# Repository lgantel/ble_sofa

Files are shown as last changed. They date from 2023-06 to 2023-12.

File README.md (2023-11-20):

# BLE Sofa
Control module for CIAR sofa using custom BLE interface.

## Overview

The sofa command box is powered over a 4 pins RJ9 connector. The voltage measured at the command box input is 29V. It is provided by the motor (LM35_05) which gets its power from the PS10 adapter (29V - 2A).

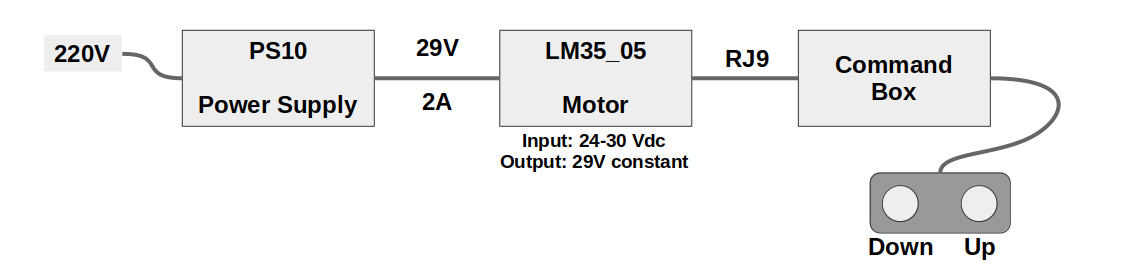
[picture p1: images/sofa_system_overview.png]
Sofa System Overview


The command box has three cable inputs:
- The RJ9 connector for power supply and motor commands
- The left input (J1) connected to the sensitive button; It corresponds to the Down command.
- The right input (J3) connected to the other sensitive button; It corresponds to the Up command.

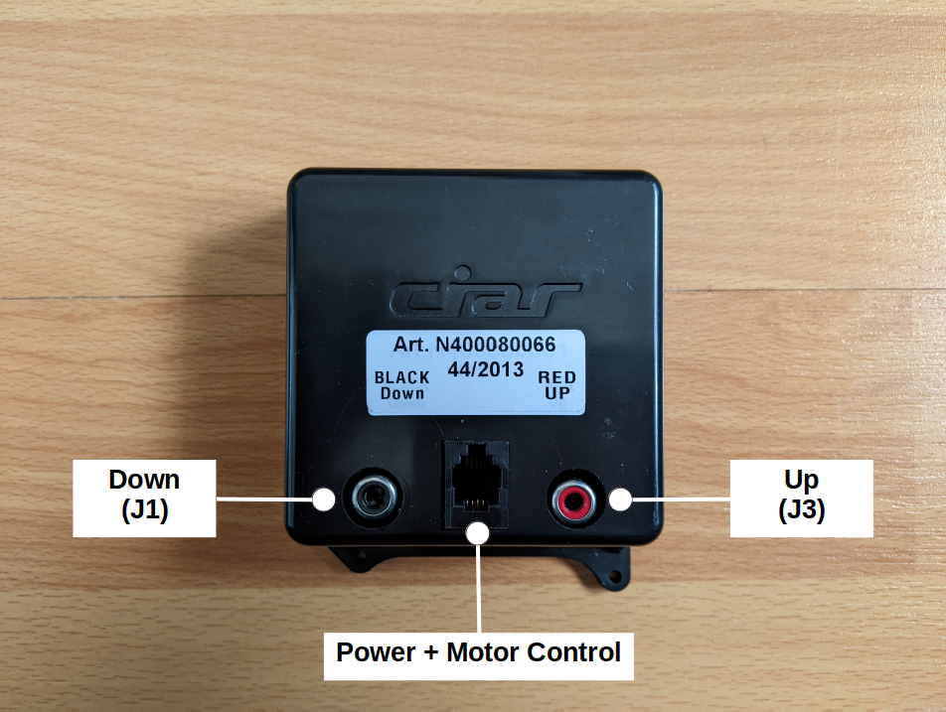
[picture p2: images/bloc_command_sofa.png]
Bloc Command Sofa


## Power Supply and Motor Commands

The RJ9 connector provides 4 wires connection which supplies power from the motor to the control box, and Up and Down commands from the control box to the motor.

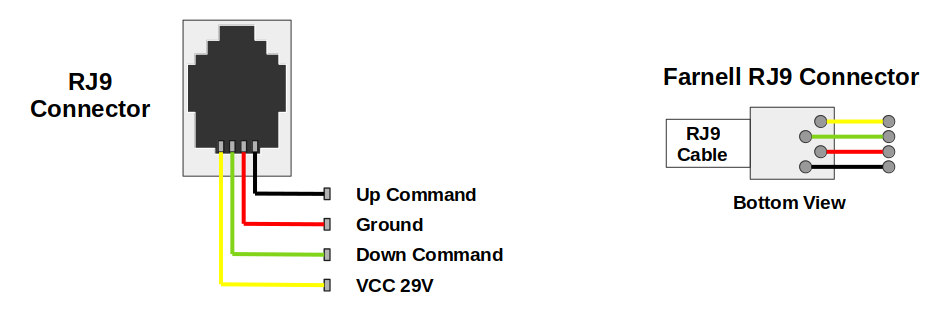
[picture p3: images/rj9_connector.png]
RJ9 Connector


## Issue with the current system

Currently the command box is connected to the Up and Down button with electrical wires. The issue comes when moving the sofa up and down, the cables are compressed by the mechanical part and end up being damaged.

## Replacement Solution

A replacement solution has been specified to allow the user to control the sofa using a wireless BLE application. The system would be based on a Raspberry Pi Pico W module which permits to easily control the motor through two electrical relays, and to receive commands from the user via the Bluetooth stack.

<p float="left">
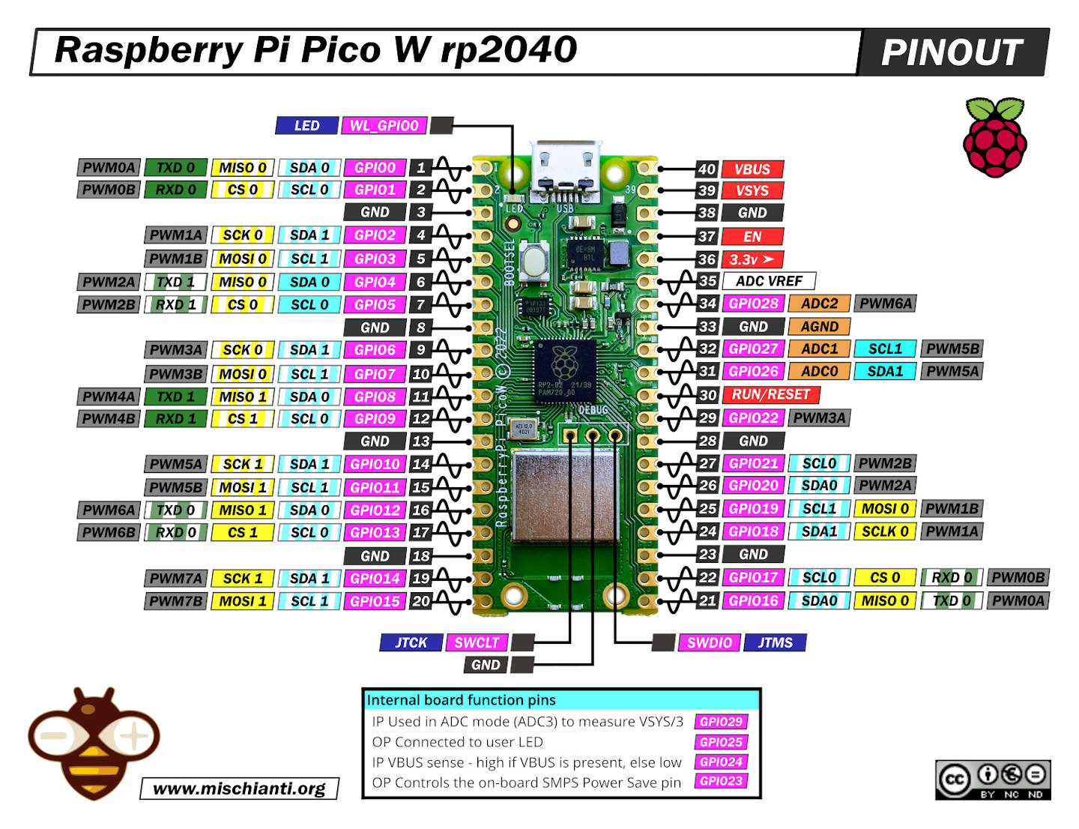
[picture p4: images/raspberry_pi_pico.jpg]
Raspberry Pi Pico W
  
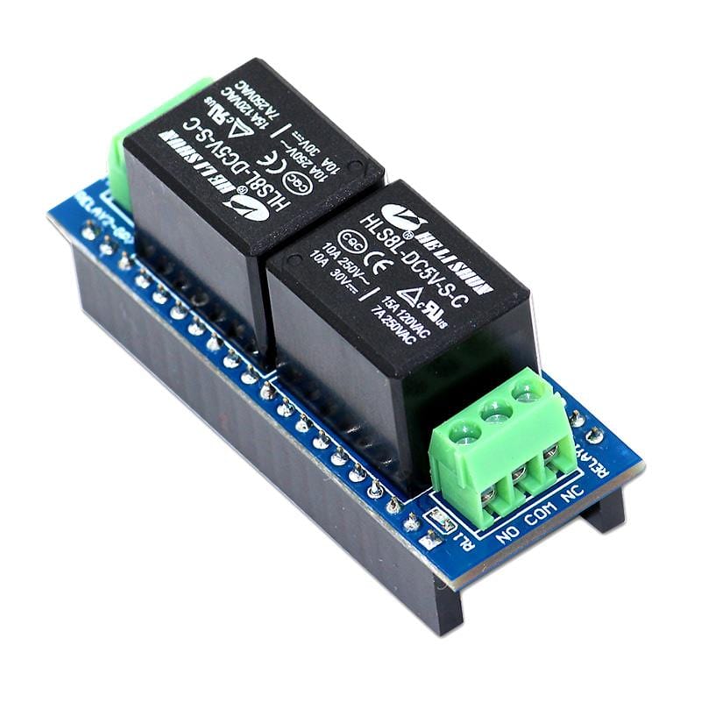
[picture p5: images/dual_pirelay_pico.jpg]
Dual PiRelay for RPi Pico
  
</p>

# Tools Setup

## Get the SDK and examples

```bash
cd pico
git clone https://github.com/raspberrypi/pico-sdk.git --branch master
cd pico-sdk
git submodule update --init
cd ..
git clone https://github.com/raspberrypi/pico-examples.git --branch master
```

## Install the toolchain

```bash
sudo apt update
sudo apt install cmake gcc-arm-none-eabi libnewlib-arm-none-eabi build-essential libstdc++-arm-none-eabi-newlib
```

In the bashrc file, export the path to the SDK:
```bash
#
# RPi Pico SDK
#
export PICO_SDK_PATH=/home/laurent/Projects/lgantel/ble_sofa/pico/pico-sdk
```

# Example Projects

```bash
cd pico/workspace
mkdir build
cd build
```

The following examples can be built:

- [LED Control](doc/example_projects.md#led-control)
- [BLE Control](doc/example_projects.md#ble-control)
- [Relay Control](doc/example_projects.md#relay-control)

# BLE Sofa Application

- [BLE Sofa Application Documentation](doc/ble_sofa_app.md#ble_sofa_app)

# Resources

## Raspberry Pi Pico

* Raspberry Pi Pico power pins information:

https://dronebotworkshop.com/pi-pico/

* A nice development kit PCB example for Raspberry Pi Pico:

https://01001000.xyz/2021-02-13-Raspberry-Pi-Pico-dev-board-Kiwikit/

* C library for LCD OLED:

https://github.com/martinkooij/pi-pico-ss-oled

* Information on the debug probes:

https://www.framboise314.fr/tout-nouveau-la-sonde-de-debogage-raspberry-pi-debug-probe/

* Kicad symbol and footprint models:

https://github.com/bdubs-astro/Raspberry_Pi_Pico_W_Kicad_Files

## Bluetooth Low Energy

* Bluetooth BLE resources:

http://tvaira.free.fr/bts-sn/activites/activite-ble/bluetooth-ble.html#gatt-et-att

https://novelbits.io/bluetooth-gatt-services-characteristics/

https://www.jaredwolff.com/get-started-with-bluetooth-low-energy/

https://punchthrough.com/android-ble-guide/

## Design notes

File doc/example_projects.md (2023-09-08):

# Example Projects

## LED Control

### Block Diagram

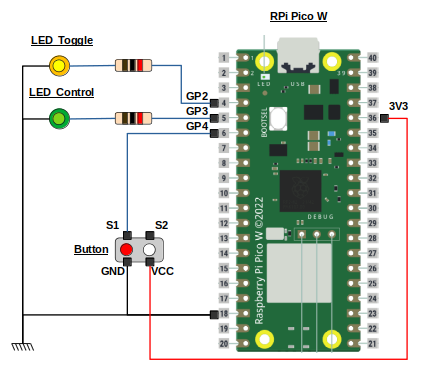
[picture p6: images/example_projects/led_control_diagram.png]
LED Control Diagram


### Description

- LED_Toggle is controlled via GP2 and is toggled every 500 ms.
- LED_Control is controlled via GP3 and its status is dependent of the state of the S1 button. In our case, the S1 button is active-low.

### Compilation

```bash
cmake ..
make -j4 led_control
```

## BLE Control

### Block Diagram

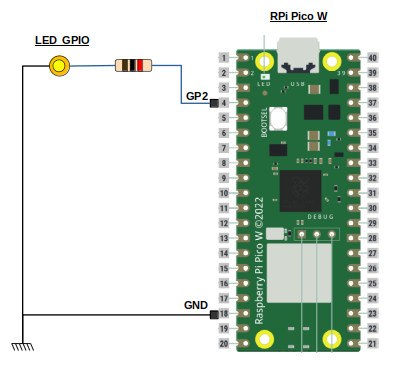
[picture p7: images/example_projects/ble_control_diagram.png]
BLE Control Diagram


### Description

In this example project, the BLE stack is activated and a GATT profile is provided by the Raspberry Pi Pico.

### Compilation

```bash
cmake -DPICO_BOARD=pico_w ..
make -j4 ble_control
```

### Test

1. Test detection on Linux

Scan of the available BLE devices:
```bash
sudo hcitool lescan
LE Scan ...
43:43:A2:12:1F:AC ble-control
```

2. Connection in interactive mode to the BLE Control device:
```bash
sudo gatttool -b 43:43:A2:12:1F:AC -I
[43:43:A2:12:1F:AC][LE]> connect
Attempting to connect to 43:43:A2:12:1F:AC
Connection successful
```

3. Read the primary services provided by the BLE Control device. Our custom service has the UUID 0000ff10-0000-1000-8000-00805f9b34fb. It defines a characteristic that can be written to control the LED state (UUID 0000ff11-0000-1000-8000-00805f9b34fb):
```bash
> primary
attr handle: 0x0001, end grp handle: 0x0003 uuid: 00001800-0000-1000-8000-00805f9b34fb  <-- Generic Access Profile
attr handle: 0x0004, end grp handle: 0x0006 uuid: 0000ff10-0000-1000-8000-00805f9b34fb  <-- Our control service
> char-desc 0x0001
handle: 0x0001, uuid: 00002800-0000-1000-8000-00805f9b34fb  <-- Primary service
handle: 0x0002, uuid: 00002803-0000-1000-8000-00805f9b34fb  <-- Characteristic information
handle: 0x0003, uuid: 00002a00-0000-1000-8000-00805f9b34fb  <-- Generic Access service (name)
handle: 0x0004, uuid: 00002800-0000-1000-8000-00805f9b34fb  <-- Primary service
handle: 0x0005, uuid: 00002803-0000-1000-8000-00805f9b34fb  <-- Characteristic information
handle: 0x0006, uuid: 0000ff11-0000-1000-8000-00805f9b34fb  <-- LED control custom characteristic
```

4. The value of the characteristic can be read with the char-read-hnd command:
```bash
char-read-hnd 0x0006
Characteristic value/descriptor: 00
```

5. The characteristic being a write-without-response characteristic, we use the char-write-cmd command to write on it:
```bash
# Set the LED on
char-write-cmd 0x0006 01
# Set the LED off
char-write-cmd 0x0006 00
```

### Android Application

An Android application has been developped to test the BLE Control example via a smartphone. The application is available in android/workspace/ble_control/.

## Relay Control

### Block Diagram

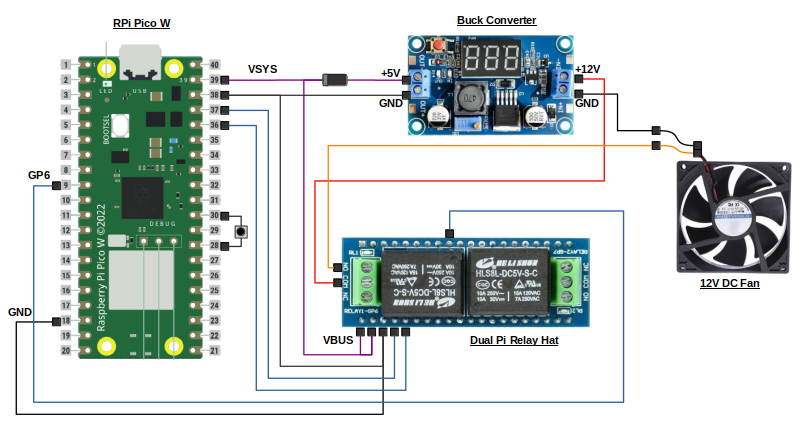
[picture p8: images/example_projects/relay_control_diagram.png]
Relay Control Diagram


### Description

In this example project, the Raspberry Pi Pico controls the relay 1 of the Dual Pi Relay Hat via the GPIO 6. 
- The relay is connected to a 12V DC fan
- The relay is turned on during 5 seconds
- The relay is then turned off for 3 seconds

### Compilation

```bash
cmake -DPICO_BOARD=pico_w ..
make -j4 relay_control
```

### References

- Pico Dual Channel Relay Hat

Information about the relay hat can be found here:

[https://learn.sb-components.co.uk/Pico-Dual-Channel-Relay-Hat]

and there:

[https://github.com/sbcshop/Pico-dual-channel-Relay-HAT]

- Known Issues with Relays:

[https://electronics.stackexchange.com/questions/631931/ac-current-on-relay-causes-pi-pico-to-reboot-continuously]

[https://forums.raspberrypi.com/viewtopic.php?t=322133]

[https://forums.raspberrypi.com/viewtopic.php?t=64595]

[https://forums.raspberrypi.com/viewtopic.php?f=91&t=83372&p=1225448#p1225448]

- Circuit for 29v to 5v converter:

[https://electronics.stackexchange.com/questions/588770/logic-level-converter-from-29v-to-5v-schematic]

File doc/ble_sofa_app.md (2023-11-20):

# BLE Sofa Application

## Block Diagram

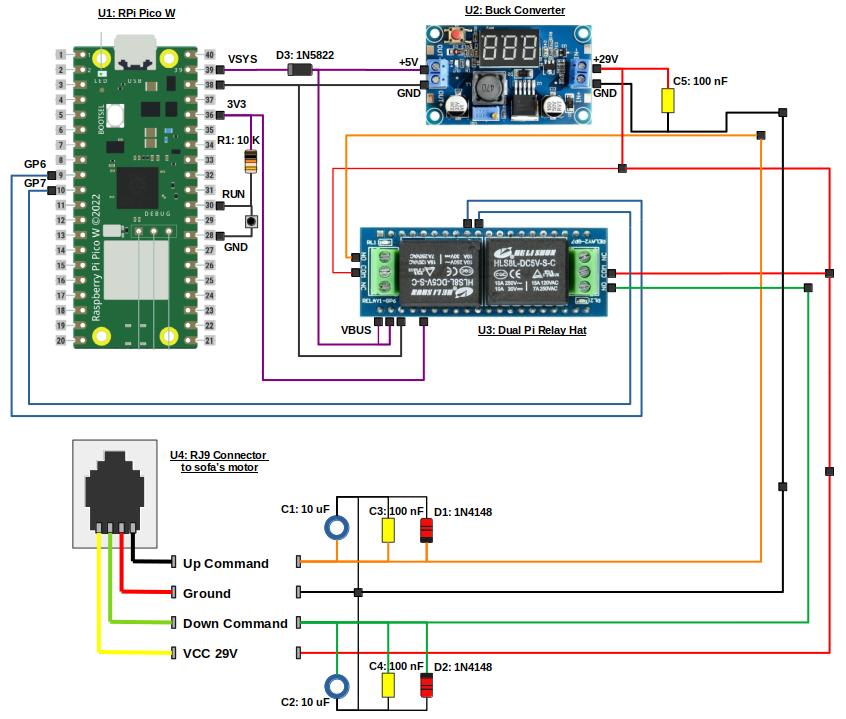
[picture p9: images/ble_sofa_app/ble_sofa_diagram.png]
BLE Sofa Diagram


## Description

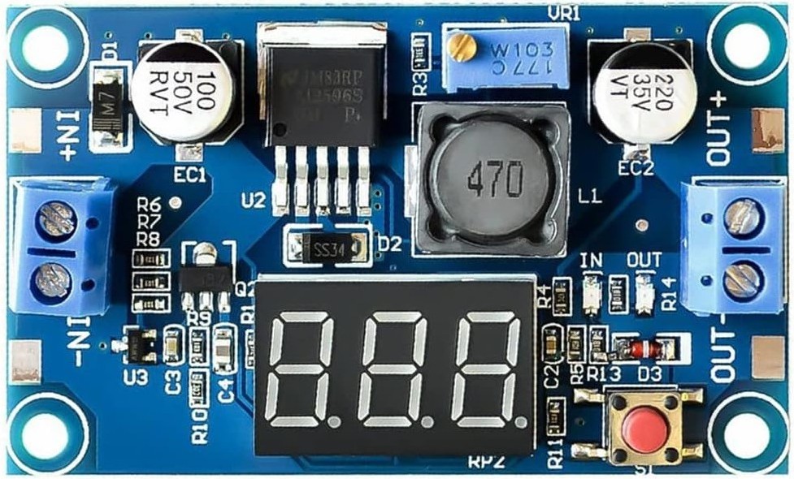
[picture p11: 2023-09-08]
images/buck_converter.jpg

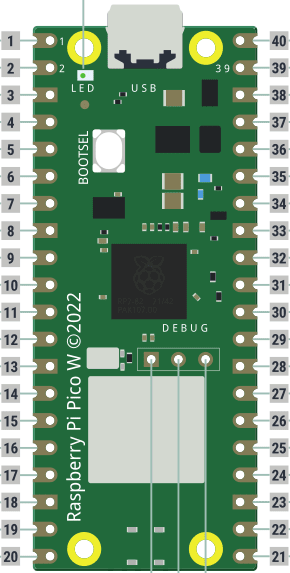
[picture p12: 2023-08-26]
images/RPi-Pico-W.png

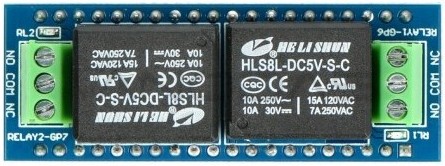
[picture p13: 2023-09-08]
images/dual_pirelay_pico_top.jpg

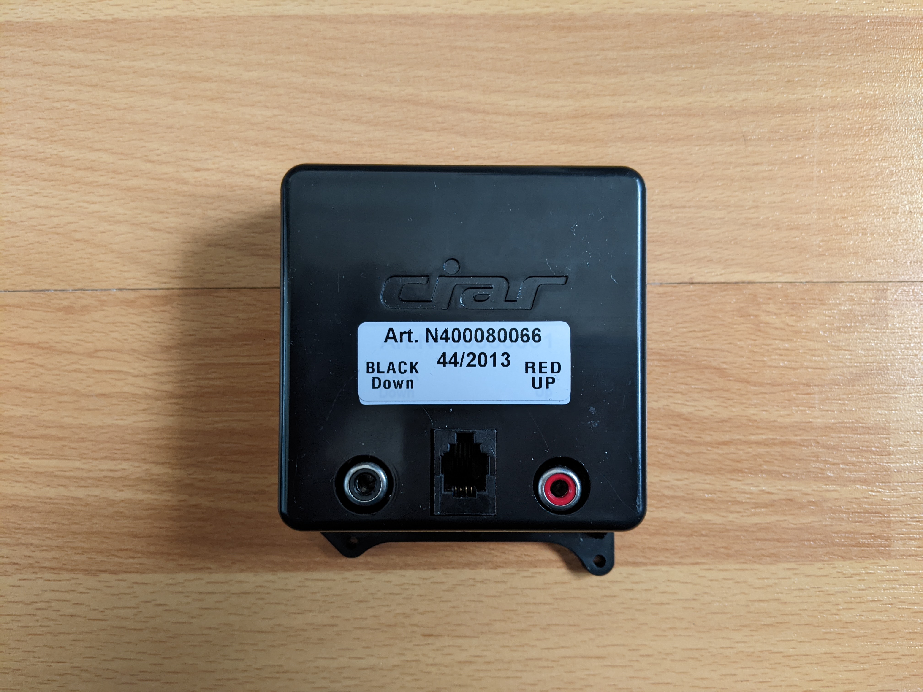
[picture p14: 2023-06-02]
images/bloc_command_sofa_orig.jpg

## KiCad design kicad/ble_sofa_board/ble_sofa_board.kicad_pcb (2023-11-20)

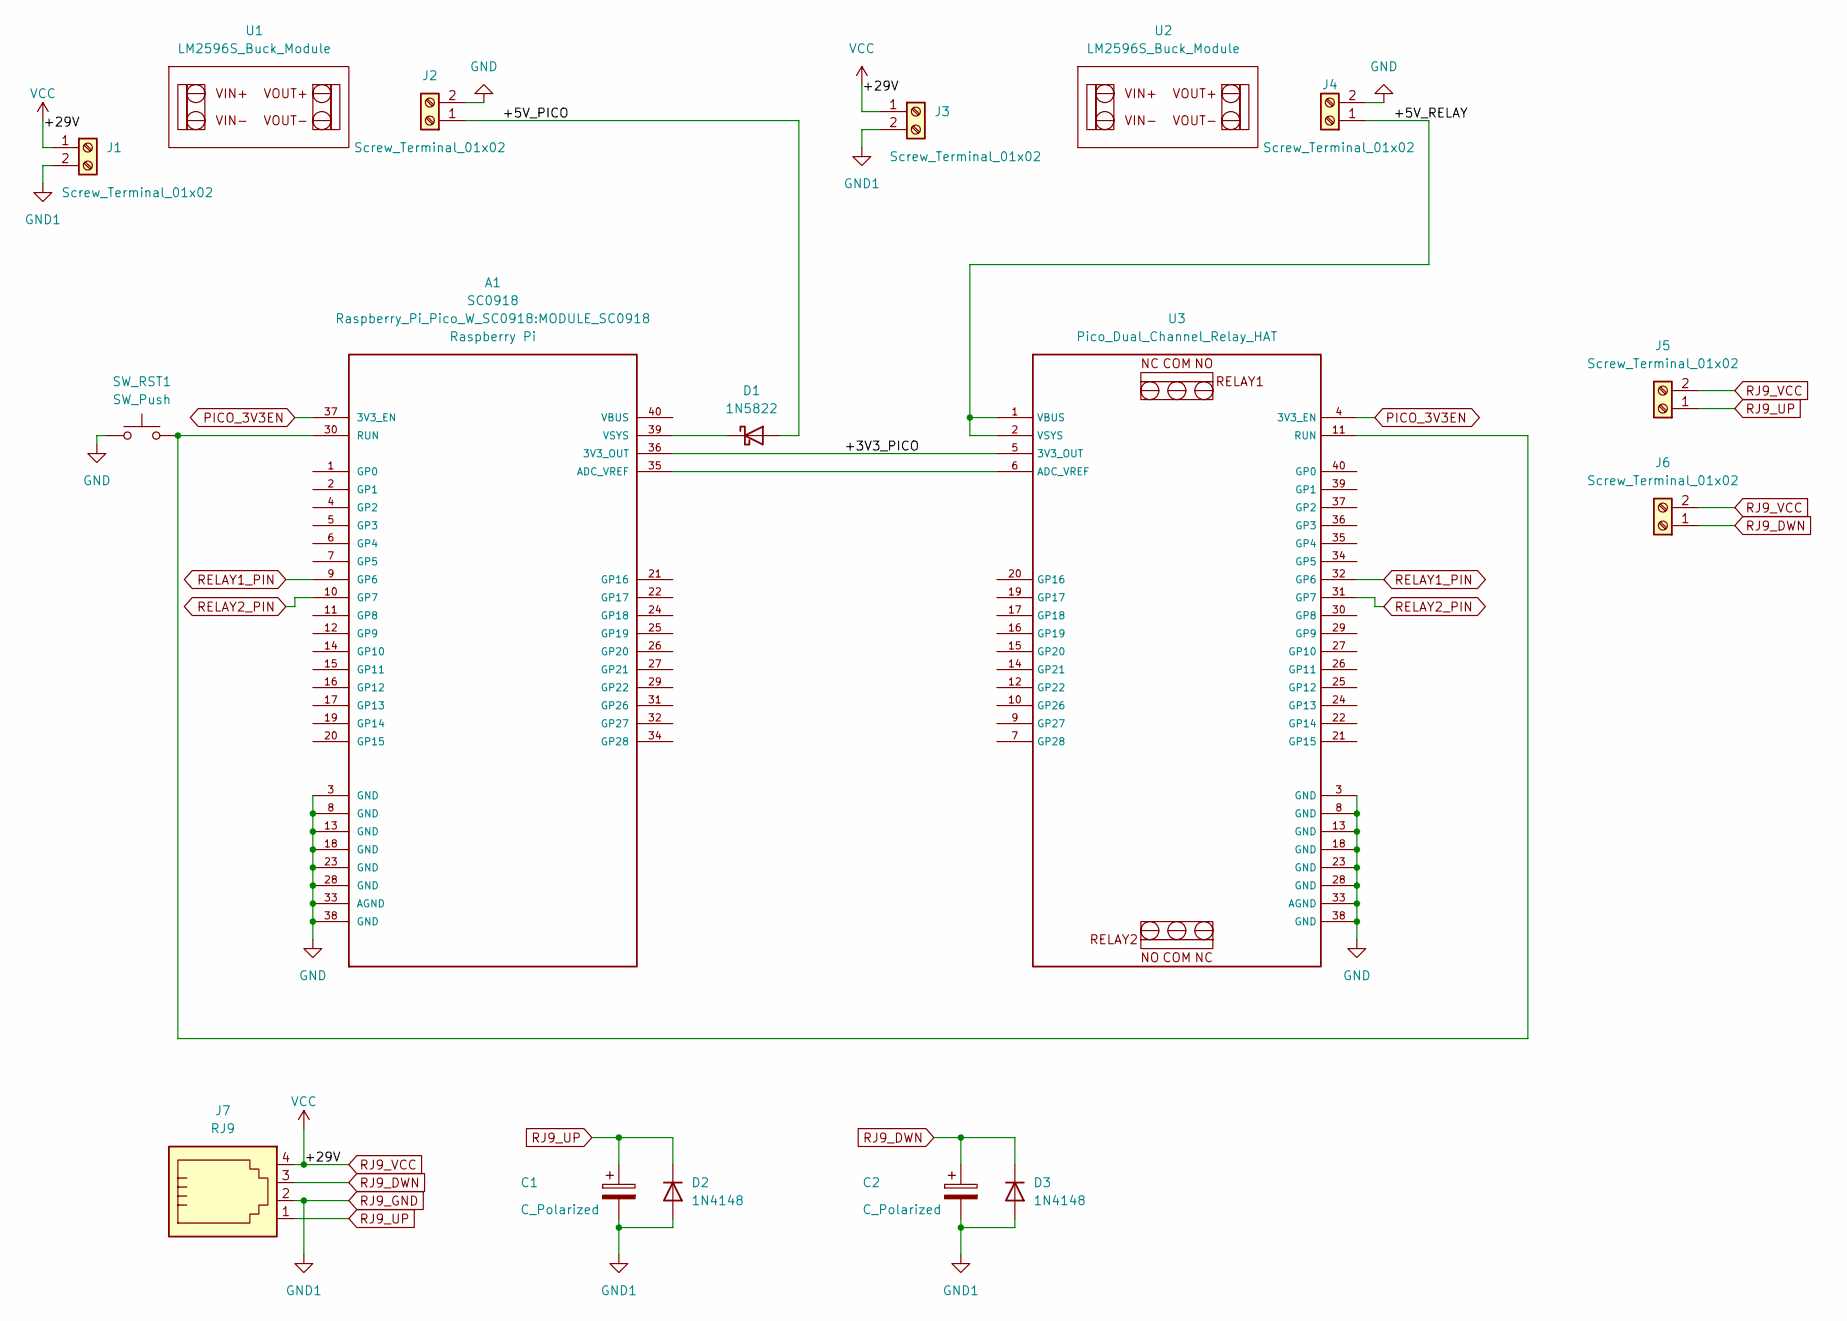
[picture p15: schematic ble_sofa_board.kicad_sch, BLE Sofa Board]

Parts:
A1: SC0918; MODULE_SC0918; PARTREV 1.6
C1, C2: C_Polarized; CP_Radial_D5.0mm_P2.50mm
D1: 1N5822; D_DO-201AD_P15.24mm_Horizontal
D2, D3: 1N4148; D_DO-35_SOD27_P7.62mm_Horizontal
J1, J2, J3, J4, J5, J6: Screw_Terminal_01x02; TerminalBlock_bornier-2_P5.08mm
J7: RJ9; 4P4C_narrow
SW_RST1: SW_Push; SW_PUSH_6mm_H4.3mm
U1, U2: LM2596S_Buck_Module
U3: Pico_Dual_Channel_Relay_HAT

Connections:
/+3V3_PICO: A1.36 (3V3_OUT), U3.5 (3V3_OUT)
/+5V_PICO: D1.2 (A), J2.1
/+5V_RELAY: J4.1, U3.1 (VBUS), U3.2 (VSYS)
GND: A1.3 (GND), A1.8 (GND), A1.13 (GND), A1.18 (GND), A1.23 (GND), A1.28 (GND), A1.33 (AGND), A1.38 (GND), J2.2, J4.2, SW_RST1.1, U3.3 (GND), U3.8 (GND), U3.13 (GND), U3.18 (GND), U3.23 (GND), U3.28 (GND), U3.33 (AGND), U3.38 (GND)
unnamed: A1.30 (RUN), SW_RST1.2, U3.11 (RUN)
unnamed: A1.35 (ADC_VREF), U3.6 (ADC_VREF)
unnamed: A1.39 (VSYS), D1.1 (K)
PICO_3V3EN: A1.37 (3V3_EN), U3.4 (3V3_EN)
RELAY1_PIN: A1.9 (GP6), U3.32 (GP6)
RELAY2_PIN: A1.10 (GP7), U3.31 (GP7)
RJ9_DWN: C2.1, D3.1 (K), J6.1, J7.3
RJ9_GND: C1.2, C2.2, D2.2 (A), D3.2 (A), J1.2, J3.2, J7.2
RJ9_UP: C1.1, D2.1 (K), J5.1, J7.1
RJ9_VCC: J1.1, J3.1, J5.2, J6.2, J7.4

Board: 2 copper layers, 17 parts (0 on the bottom side), 14 nets, no tracks yet.

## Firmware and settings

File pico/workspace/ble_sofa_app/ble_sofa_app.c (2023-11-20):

/*--------------------------------------------------------------------------------  
--                          _               _       _ 
--                         | |__ _ __ _ _ _| |_ ___| |
--                         | / _` / _` | ' \  _/ -_) |
--                         |_\__, \__,_|_||_\__\___|_|
--                           |___/                                        
--
----------------------------------------------------------------------------------
--
-- Company: LGANTEL
-- Engineer: Laurent Gantel <laurent.gantel@gmail.com>
--
-- Project Name: BLE Sofa Application
-- Version: 0.1.0
-- File Name: ble_sofa_app.c
-- Description: Control of two relays via BLE to turn on/off two 12V DC fans
--
-- Last update: 2023-09-24
--
-------------------------------------------------------------------------------*/

#include <stdio.h>

#include "btstack_run_loop.h"
#include "pico/stdlib.h"
#include "btstack_event.h"
#include "pico/cyw43_arch.h"
#include "pico/btstack_cyw43.h"
#include "btstack.h"
#include "ble/gatt-service/nordic_spp_service_server.h"
#include "mygatt.h"

#include "relay.h"

//----------------------------------------------------------------
// Constants
//----------------------------------------------------------------

#define WL_LED_GPIO  0

#define RELAY1_GPIO   6
#define RELAY2_GPIO   7

// Global variables

/** @brief Structure to control Relay1 */
relay_t relay1;

/** @brief Structure to control Relay2 */
relay_t relay2;

//----------------------------------------------------------------------------------
// Bluetooth variables
//----------------------------------------------------------------------------------

#define REPORT_INTERVAL_MS 3000
#define MAX_NR_CONNECTIONS 3 

/** @brief LED Command characteristic */
#define ATT_CHARACTERISTIC_0000FF11_VALUE_HANDLE 0x0006

/** @brief Advertisements information */
const uint8_t adv_data[] = {
    2, BLUETOOTH_DATA_TYPE_FLAGS, 0x06, 
    9, BLUETOOTH_DATA_TYPE_COMPLETE_LOCAL_NAME, 'b', 'l', 'e','-', 's', 'o', 'f', 'a',
    // Incomplete List of 16-bit Service Class UUIDs -- FF10 - only valid for testing!
    3, BLUETOOTH_DATA_TYPE_INCOMPLETE_LIST_OF_16_BIT_SERVICE_CLASS_UUIDS, 0x10, 0xff,
};
const uint8_t adv_data_len = sizeof(adv_data);

/** @brief HCI registration callback */
static btstack_packet_callback_registration_t hci_event_callback_registration;

// Data: command the relays status:
//   - bit [0]: '0' = Relay1 OFF, '1' = Relay1 ON
//   - bit [1]: '0' = Relay2 OFF, '1' = Relay2 ON
static uint8_t data = 0x00;
static int data_len = 1; // Data length in byte

//----------------------------------------------------------------------------------
// Bluetooth static functions
//----------------------------------------------------------------------------------

// Prototypes
static void hci_packet_handler(uint8_t packet_type, uint16_t channel, uint8_t *packet, uint16_t size);
static uint16_t att_read_callback(hci_con_handle_t con_handle, uint16_t att_handle, uint16_t offset, uint8_t * buffer, uint16_t buffer_size);
static int att_write_callback(hci_con_handle_t con_handle, uint16_t att_handle, uint16_t transaction_mode, uint16_t offset, uint8_t *buffer, uint16_t buffer_size);
static void att_packet_handler(uint8_t packet_type, uint16_t channel, uint8_t *packet, uint16_t size);

/**
 * @brief Host Controller Interface (HCI) Packet Handler
 * 
 * @param packet_type 
 * @param channel 
 * @param packet 
 * @param size 
 */
static void hci_packet_handler(uint8_t packet_type, uint16_t channel, uint8_t *packet, uint16_t size) {
  UNUSED(channel);
  UNUSED(size);

  uint16_t conn_interval;
  hci_con_handle_t con_handle;

  if (packet_type != HCI_EVENT_PACKET) { return; }

  switch (hci_event_packet_get_type(packet)) {
    case BTSTACK_EVENT_STATE:
      // BTstack activated, get started
      if (btstack_event_state_get_state(packet) == HCI_STATE_WORKING) {
        printf("> BLE Control - BTstack activated\n");
      }
      break;
    case HCI_EVENT_LE_META:
      switch (hci_event_le_meta_get_subevent_code(packet)) {
        case HCI_SUBEVENT_LE_CONNECTION_COMPLETE:
          // Print connection parameters (without using float operations)
          con_handle = hci_subevent_le_connection_complete_get_connection_handle(packet);
          conn_interval = hci_subevent_le_connection_complete_get_conn_interval(packet);
          printf("LE Connection - Connection Interval: %u.%02u ms\n", conn_interval * 125 / 100, 25 * (conn_interval & 3));
          printf("LE Connection - Connection Latency: %u\n", hci_subevent_le_connection_complete_get_conn_latency(packet));

          // Request min con_interval 15ms for iOS 11+
          printf("LE Connection - Request 15 ms connection interval\n");
          gap_request_connection_parameter_update(con_handle, 12, 12, 0, 0x0048);
          break;
        case HCI_SUBEVENT_LE_CONNECTION_UPDATE_COMPLETE:
          // Print connection parameters (without using floating point operations)
          con_handle    = hci_subevent_le_connection_update_complete_get_connection_handle(packet);
          conn_interval = hci_subevent_le_connection_update_complete_get_conn_interval(packet);
          printf("LE Connection - Connection Param update - connection interval %u.%02u ms, latency %u\n", 
                    conn_interval * 125 / 100,
                    25 * (conn_interval & 3), hci_subevent_le_connection_update_complete_get_conn_latency(packet));
          break;
        default:
          break;
      }
      break;
    default:
      break;
  }
}

/**
 * @brief ATT client read callback
 * 
 * @param connection_handle 
 * @param att_handle 
 * @param offset 
 * @param buffer 
 * @param buffer_size 
 * @return uint16_t 
 */
static uint16_t att_read_callback(hci_con_handle_t connection_handle, uint16_t att_handle, uint16_t offset, uint8_t * buffer, uint16_t buffer_size){
    UNUSED(connection_handle);

    //printf("> att_read_callback: att_handle %04x, offset %04x, buff size %04x\n", att_handle, offset, buffer_size);

    if (att_handle == ATT_CHARACTERISTIC_0000FF11_VALUE_HANDLE) {
        return att_read_callback_handle_blob((const uint8_t *)&data, data_len, offset, buffer, buffer_size);
    }

    return 0;
}

/**
 * @brief ATT client write callback
 * 
 * @param connection_handle 
 * @param att_handle 
 * @param transaction_mode 
 * @param offset 
 * @param buffer 
 * @param buffer_size 
 * @return int 
 */
static int att_write_callback(hci_con_handle_t connection_handle, uint16_t att_handle, uint16_t transaction_mode, uint16_t offset, uint8_t *buffer, uint16_t buffer_size){
    UNUSED(connection_handle);
    UNUSED(transaction_mode);
    UNUSED(offset);
    UNUSED(buffer_size);

    //printf("> att_write_callback: att_handle %04x, offset %04x, buff size %04x\n", att_handle, offset, buffer_size);
    if ((buffer == NULL) || (att_handle != ATT_CHARACTERISTIC_0000FF11_VALUE_HANDLE)) { return 0; }

    // Update data
    data = *buffer;
    //printf("> Update data\t- data = %02x\n", data);

    // Process data
    // - Bit [0] is used to set Relay1 on/off
    if (data & 0x01) { relay_on(&relay1); } else { relay_off(&relay1); }
    // - Bit [1] is used to set Relay2 on/off
    if (data & 0x02) { relay_on(&relay2); } else { relay_off(&relay2); }
    
    return 0;
}

/**
 * @brief Attribute Protocol (ATT) Packet Handler
 * 
 * @param packet_type 
 * @param channel 
 * @param packet 
 * @param size 
 */
static void att_packet_handler(uint8_t packet_type, uint16_t channel, uint8_t *packet, uint16_t size) {
  UNUSED(channel);
  UNUSED(size);
    
  if (packet_type != HCI_EVENT_PACKET) return;

  switch (hci_event_packet_get_type(packet)) {
    case ATT_EVENT_CONNECTED:
      printf("Connected\n");
      break;
    case ATT_EVENT_DISCONNECTED:
      printf("Disconnected\n");
      break;
    default:
      break;
  }
}

//----------------------------------------------------------------
// Functions
//----------------------------------------------------------------

/**
 * @brief Main entry point
 * @return int Endless loop, never returns
 */
int main(void)
{
    // Initialize the relays output
    relay_init(&relay1, RELAY1_GPIO);
    relay_init(&relay2, RELAY2_GPIO);

    // Turn off relay 1
    relay_off(&relay1);
    // Turn off relay 2
    relay_off(&relay2);

    // Wait a moment
    sleep_ms(2000);

    // Initialize the Bluetooth stack
    if (cyw43_arch_init()) return -1;

    // Turn off the wireless LED
    cyw43_arch_gpio_put(WL_LED_GPIO, false);

    // Initialize the Logical Link Control and Adaptation Layer Protocol (L2CAP) layer
    l2cap_init();
    // Initialize Security Manager (SM)
    sm_init();
    // Initialize Attribute Protocol
    att_server_init(profile_data, att_read_callback, att_write_callback);

    // Setup advertisements
    uint16_t adv_int_min = 0x0030;
    uint16_t adv_int_max = 0x0030;
    uint8_t adv_type = 0;
    bd_addr_t null_addr;
    memset(null_addr, 0, 6);
    gap_advertisements_set_params(adv_int_min, adv_int_max, adv_type, 0, null_addr, 0x07, 0x00);
    gap_advertisements_set_data(adv_data_len, (uint8_t *) adv_data);
    gap_advertisements_enable(true);

    // Register HCI events callback
    hci_event_callback_registration.callback = &hci_packet_handler;
    hci_add_event_handler(&hci_event_callback_registration);

    // Register for ATT events
    att_server_register_packet_handler(att_packet_handler);

    // Initialize data
    data = 0x00;
    data_len = 1;

    hci_power_control(HCI_POWER_ON);

    // Turn on the LED to indicate that BLE is fully initialized
    cyw43_arch_gpio_put(WL_LED_GPIO, true);

    // Endless loop
    btstack_run_loop_execute();

    return 0;
}

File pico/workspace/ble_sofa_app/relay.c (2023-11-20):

/*--------------------------------------------------------------------------------  
--                          _               _       _ 
--                         | |__ _ __ _ _ _| |_ ___| |
--                         | / _` / _` | ' \  _/ -_) |
--                         |_\__, \__,_|_||_\__\___|_|
--                           |___/                                        
--
----------------------------------------------------------------------------------
--
-- Company: LGANTEL
-- Engineer: Laurent Gantel <laurent.gantel@gmail.com>
--
-- Project Name: BLE Sofa Application
-- Version: 0.1.0
-- File Name: relay.c
-- Description: Control relay through GPIO
--
-- Last update: 2023-09-09
--
-------------------------------------------------------------------------------*/

#include "relay.h"

//----------------------------------------------------------------
// Functions
//----------------------------------------------------------------

/**
 * @file relay.h
 * @name relay_init
 */
void relay_init(relay_t * relay, uint relay_gpio) {
    // Store associated GPIO
    relay->gpio = relay_gpio;
    // Init relay
    gpio_init(relay->gpio);
    gpio_set_dir(relay->gpio, GPIO_OUT);
}

/**
 * @file relay.h
 * @name relay_on
 */
void relay_on(relay_t * relay) {
    gpio_put(relay->gpio, true);
}

/**
 * @file relay.h
 * @name relay_off
 */
void relay_off(relay_t * relay) {
    gpio_put(relay->gpio, false);
}

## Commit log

2023-06-03 tests - Add project to test LED control
2023-06-28 ble_control - Cleanup and adapt app. to remotely control a LED
2023-07-09 relay_control - Add project to test relays before BLE interfacing
2023-07-10 README - Add schema for LED Control example
2023-09-07 relay_control - Validate project and complete doc
2023-09-29 ble_sofa_app - Add RPi Pico W firmware project
2023-10-22 ble_sofa_app - WIP - Add Kicad schematics and footprints
    [ble_sofa_board.kicad_pcb, ble_sofa_board.kicad_sch]
2023-10-22 ble_sofa_app - Add Raspberry Pi Pico W symbol, footprint and 3D model
2023-11-01 ble_sofa_board - WIP schematic
    [ble_sofa_board.kicad_sch]
2023-11-12 ble_sofa_board - Complete schematic and PCB
    [ble_sofa_board.kicad_pcb, ble_sofa_board.kicad_sch]
2023-11-20 ble_sofa_board - Update gnd in diagram
2023-12-06 ble_sofa_board - diagram - update PNG image and capacitors values
2023-12-28 ble_sofa_diagram - Add 3v3 RUN pullup + buck input capacitor
